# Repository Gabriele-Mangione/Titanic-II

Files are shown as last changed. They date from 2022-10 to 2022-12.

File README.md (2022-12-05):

# TITANIC II :ship:
TITANIC II is a project for an RC boat model with paired controller made by me! :grin:

## Working principle :gear:

Both electronics are powered using 14.4V Batteries, use Arduino Nano Every(s) as μController and communicate via LoRa using two RFM69HCW modules.
The Boat uses a 12V motor to swim and a servo-motor to steer, while the transmitter sends information gathered by a joystick module. 

## Features :bulb:
The boat is equipped with:
* A water gun controlled by a servomotor when clicking on the joystick
* Adjustable PWM motor speed
* Three HC-SR04 ultrasonic sensors that prevent hard collisions through adjusting of the motor speed
* External power supply pins for implementation of further modules (i.e. solar panels)

The transmitter is equipped with:
* Joystick module for a good user interface
* A tft 128x64 monochrome display to show inputs sent to the boat and boat connection
* Comfortable 3d-printed case

## Dependencies :scroll:
The codes need the following libraries in order to work.

Boat.ino:
* RFM69 lib (Lowpowerlab)
* SPI lib (Arduino)
* Servo lib (Arduino)
* [Ultrasonicsensor lib (made by me)](https://github.com/Gabriele-Mangione/UltrasonicSensor_lib)
  * you can find this in [my GitHub Repositories](https://github.com/Gabriele-Mangione?tab=repositories)

Transmitter.ino:
* GFX lib (Adafruit)
* SSD1306 lib (Adafruit)
* RFM69 lib (Lowpowerlab)
* SPI lib (Arduino)

## Contributing :pencil2:

You are welcome to make commits of suggestions for improvements.

## License :bookmark_tabs:

[MIT](https://choosealicense.com/licenses/mit/)

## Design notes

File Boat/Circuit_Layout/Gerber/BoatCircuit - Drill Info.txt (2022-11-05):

ULTIBOARD DRILL REPORT

Design: BoatCircuit

DRILL FILE SETTINGS
Excellon 2, Absolute, Metric, 3.4 

DEFINITION COPPER LAYERS
Copper Top
Copper Bottom

--------------------------------------------------------------------

DRILLFILE                                    LAMINATION
BoatCircuit - Copper Top-Copper Bottom.drl   Copper Top .. Copper Bottom

TOOL     SIZE   TYPE  COUNT
   1   3.2000   NPTH      4
   2   1.0000    PTH     72
   3   1.3208    PTH      3

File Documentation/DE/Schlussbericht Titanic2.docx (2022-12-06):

# TITANIC II

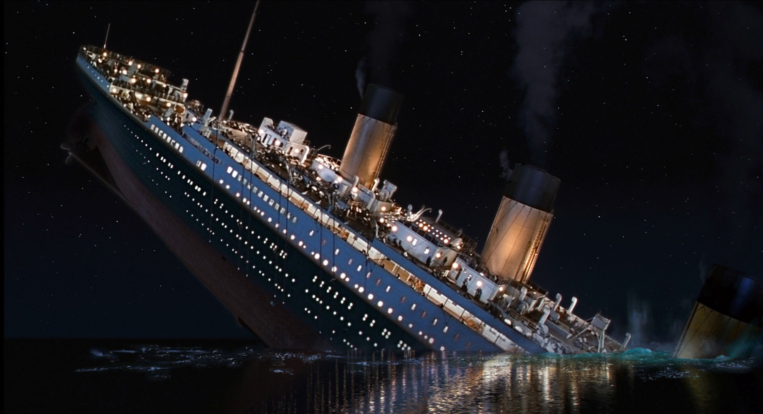
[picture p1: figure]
What's Jewish About … The Titanic? - Atlanta Jewish Times

Gabriele Mangione

ETRO 7A 2022
BüP Projekt

# Projektbeschreibung

Titanic 2 ist ein ferngesteuertes Modell-Boot. Der Rumpf besteht aus Holz und ist mit Holzlack gefertigt. Das Boot hat einen hohlen Raum, wo die ganze Elektronik installiert ist. Ein 12V Motor ist hier mit einem 3D-gedruckten Teil befestigt. Unterm Dach sind eine mechanische Pumpe und ein Servomotor befestigt, sodass die Umdrehung vom Servomotor, Wasser aus der Pumpe schiessen lässt. Ein zweiter Servomotor ist beim Heck des Bootes befestigt und steuert die Ruder. Beim Bug sind drei Ultraschallsensoren montiert, die die Distanz in drei verschiedene Richtungen messen. Ist die gemessene Distanz kleiner als 50 cm, wird die Geschwindigkeit vom Boot auf 20% der Eingabe beschränkt.

Der Transmitter vom Boot wurde 3D-Gedruckt und hat einen Joystick und ein Display als UI. Durch die Bewegung vom Joystick wird auf der Y-Achse die PWM vom Motor gesteuert und Auf der X-Achse die Steuerrichtung durch das Ruder eingestellt. Beim Klicken vom Joystick wird ein Wasserstrahl vom Boot-Dach geworfen. Aufs Display werden die Steuereingänge vom Joystick angezeigt, sowie die drei gemessenen Distanzen der Ultraschallsensoren.

## Merkmale

- Motor mit PWM
- Ruder durch Servomotor steuern
- Wasserpistole
- Controller mit Joystick und Display
- Fernsteuerung durch Radiofrequenz (915MHz)

## Realisierungskonzept

### Idee

Im Fach Werken, hatte ich vor einige Jahre in der Sekundastufe ein Modellboot gebaut. Das Boot war nur mit einem Motor, ein Schalter und zwei befestigte Ruder vorgelegt. Die Idee ist es, das Boot fernsteuerbar zu machen.

### Boot Material

Das Boot hat einen Holz-Rumpf und ist mit Holzlack gefertigt. Es hat einen hohlen Raum, wo die ganze Elektronik installiert wird. Ein 12V Motor ist hier mit einem 3D-gedruckten Teil befestigt. Zwei Metall-Ruder sind beim hinteren Teil vom Boot platziert. Die Schaltung wird durch eine 14.4V Batterie mit Spannung versorgt.

### Motor mit PWM

Motor durch PWM-Ausgang vom Arduino und N-MOS steuern. Durch die PWM-Einstellung kann man die Geschwindigkeit des Motors bzw. Boot einstellen.

### Ruder durch Servomotor steuern

Die Ruder des Bootes werden durch einen Servomotor gesteuert. Sie sind mit einem Stab zusammen angeschlossen, sodass beide Rudern durch einen Servomotor gesteuert werden können.

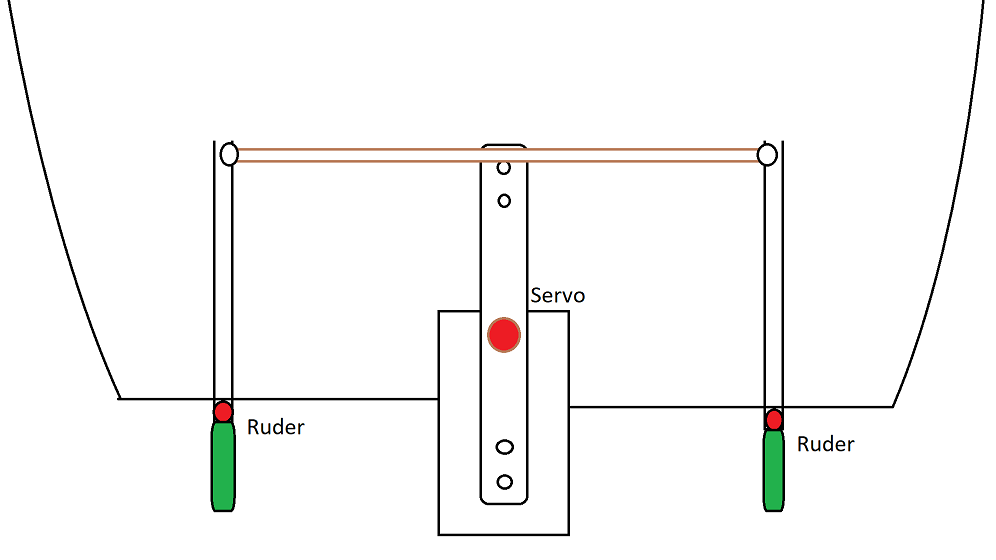
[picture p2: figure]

Abbildung 1: Ruder Mechanismus

### Wasserpistole

Für die Wasserpistole wird eine solche Pumpe verwendet:

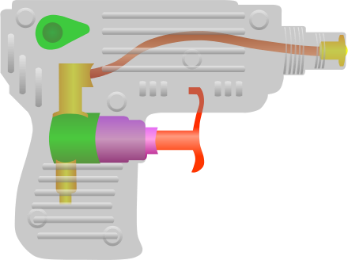
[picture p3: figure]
Water gun - Wikiwand

Abbildung 2: Pumpe Wasserpistole

An der Wassereingangsseite der Pumpe ist ein Schlauch, der ins Wasser über Bord liegt. So bekommt die Wasserpistole Flüssigkeit aus dem Wasserspiegel.

### Kommunikation

Die Kommunikation zwischen Boot und Transmitter passiert durch 915MHz Radio Module.

### Distanzsensoren

Um ungewollten Umfällen zu vermeiden, werden drei Distanzsensoren aufs Boot platziert. Falls die gemessene Distanz weniger als 50cm beträgt, wird das PWM vom Boot auf ein Fünftel vom Eingabewert beschränkt.

### Transmitter

Beim Transmitter werden ein Display und ein Joystick stehen, um das Boot zu steuern und die verschiedenen Parameter, wie PWM und Lenkwinkel angezeigt.

# Skizze zum Projekt

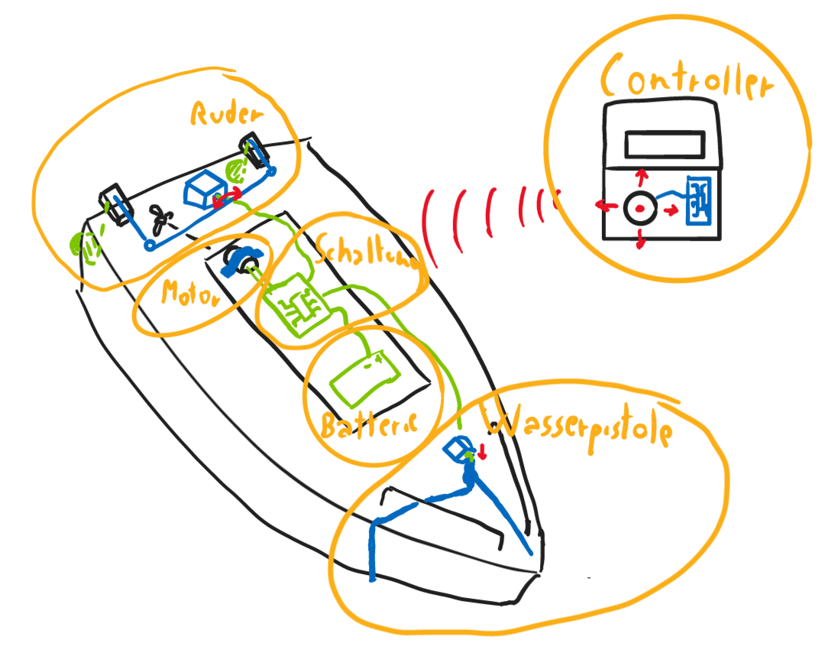
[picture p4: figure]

Abbildung 3: Projektskizze

# Blockschaltbild

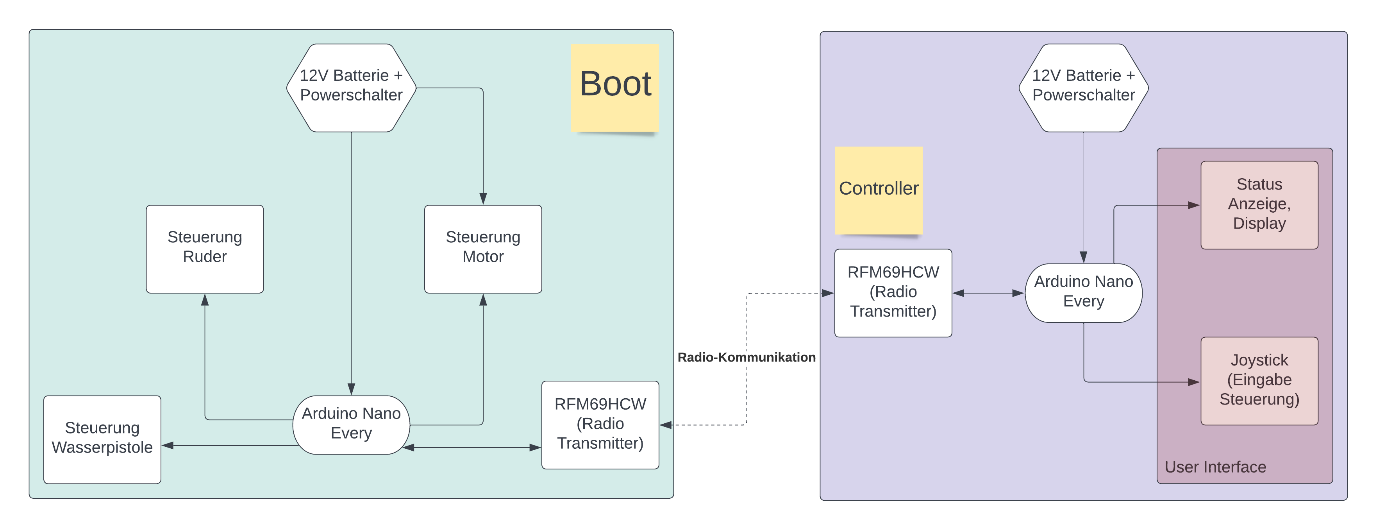
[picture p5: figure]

Abbildung 4: Blockschaltbild Architektur

# Schaltungen

## Bootschaltung

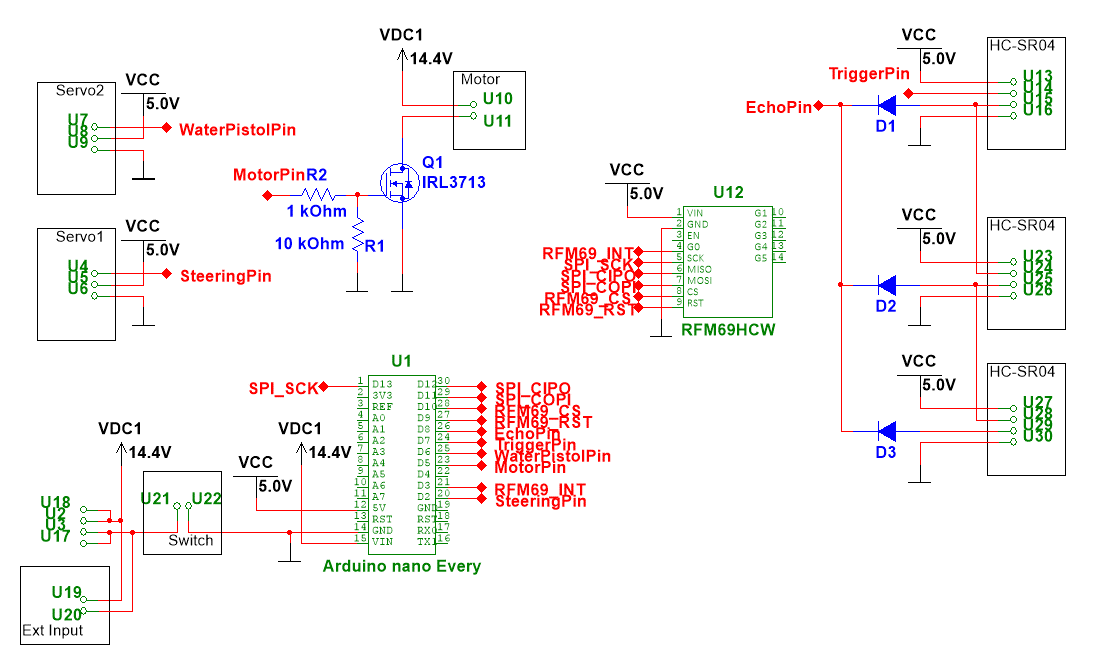
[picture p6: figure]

Abbildung 5: Bootschaltung

## Transmitterschaltung

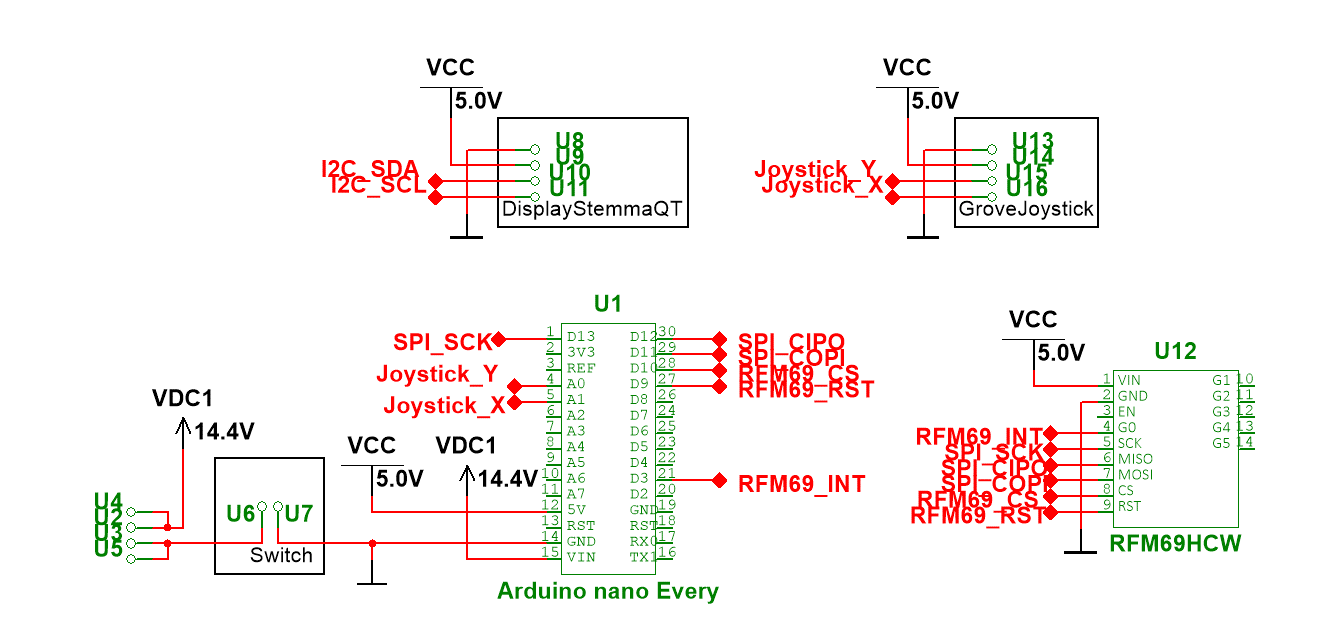
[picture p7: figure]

Abbildung 6: Transmitterschaltung

## Schaltungsbeschreibung

### Spannungsversorgung

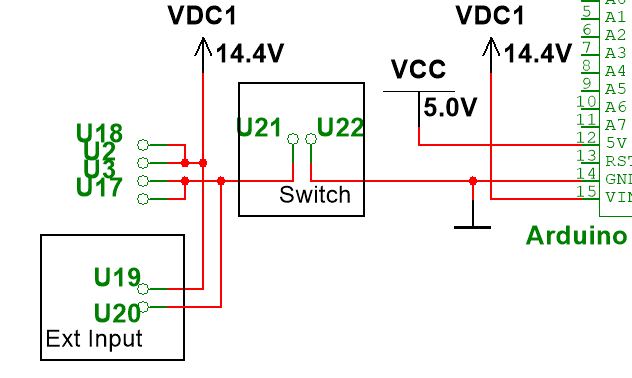
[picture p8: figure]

Abbildung 7: Spannungsversorgung Boot

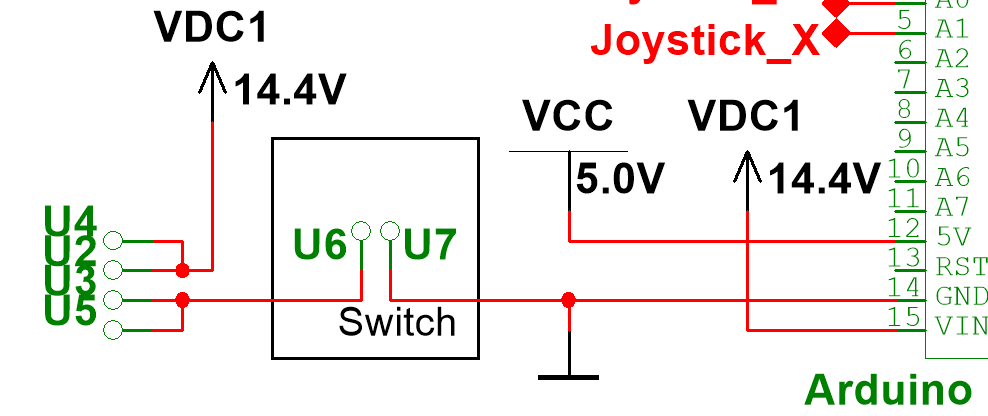
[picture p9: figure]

Abbildung 8: Spannungsversorgung Transmitter

Eine 14.4V 3200 mAh Li-Ion Batterie wird als Spannungsversorgung für die Schaltung gebraucht. Parallel zur Batterie hat es bei der Bootschaltung ein EXT Input, für eine eventuelle Power-Erweiterung, wie Solar Panels. Die Ground-Leitung wird durch einen Powerschalter getrennt, um die Schaltung manuell abschalten zu können. Die 14.4V Versorgungsspannung wird durch den im Arduino integrierten Spannungsregler auf 5.0V geregelt und beim Entsprechenden Pin vom uC ausgegeben.

### Mikrocontroller

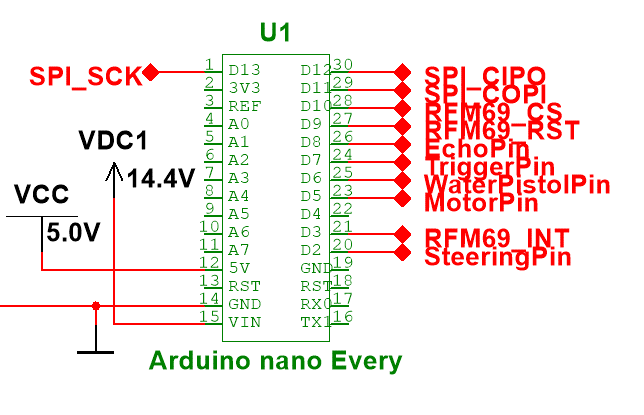
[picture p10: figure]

Abbildung 9: Schaltung Arduino Nano Every

Als Mikrocontrollereinheit werden bei den Schaltungen zwei Arduino Nano Every eingesetzt. Diese steuern die ganze Logik der Schaltungen. Siehe Code für genauere Beschreibung

### Radiomodul

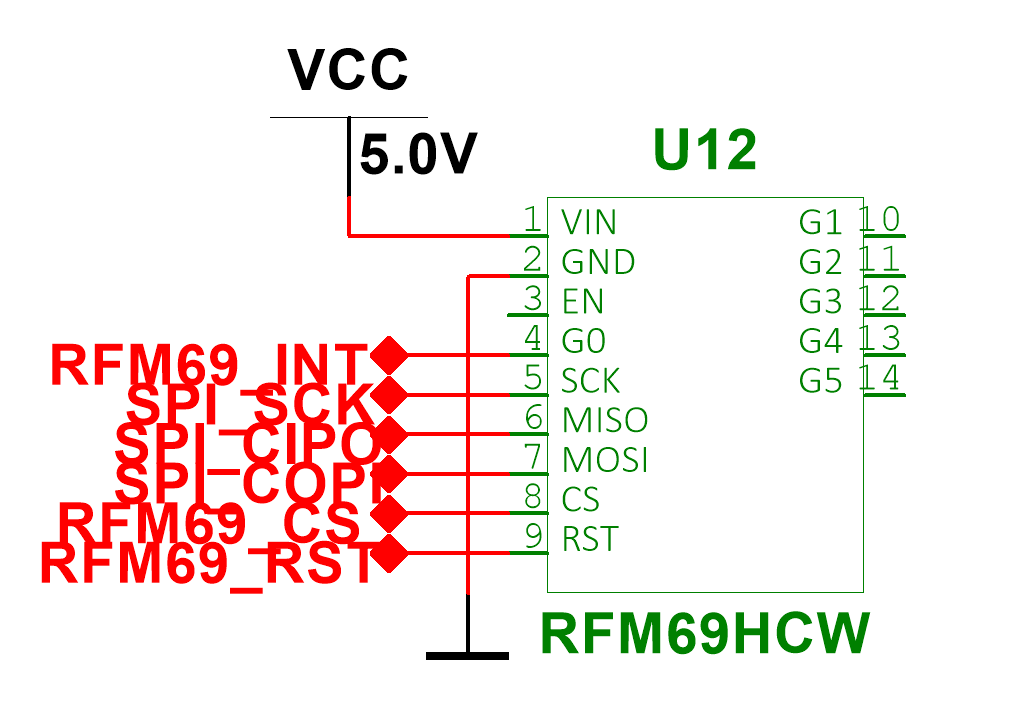
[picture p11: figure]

Abbildung 10: Radiomodul

Als Radiokommunikationsmodul wird ein RFM69HCW LoRa Radio Modul von Adafruit verwendet. Dieses Modul kommuniziert im Frequenzbereich von zwischen 868MHz und 915MHz mit bis zu 100mW Power-Output. Die Kommunikation zwischen Arduino und Radiomodul passiert durch SPI-Protokoll. Durch die RFM69_RST Leitung kann man das Modul durch einfaches Hoch- und Tiefsetzen der Spannung resetten und die RFM69_INT Leitung dient zur Synchronisierung der Operationen des Radiomodules durch Hardwareinterrupts.

Die Inputs vom Transmitter werden durch dieses Bauteil zum Boot kommuniziert und danach verarbeitet.

### Ausgangstufe Motor (Bootschaltung)

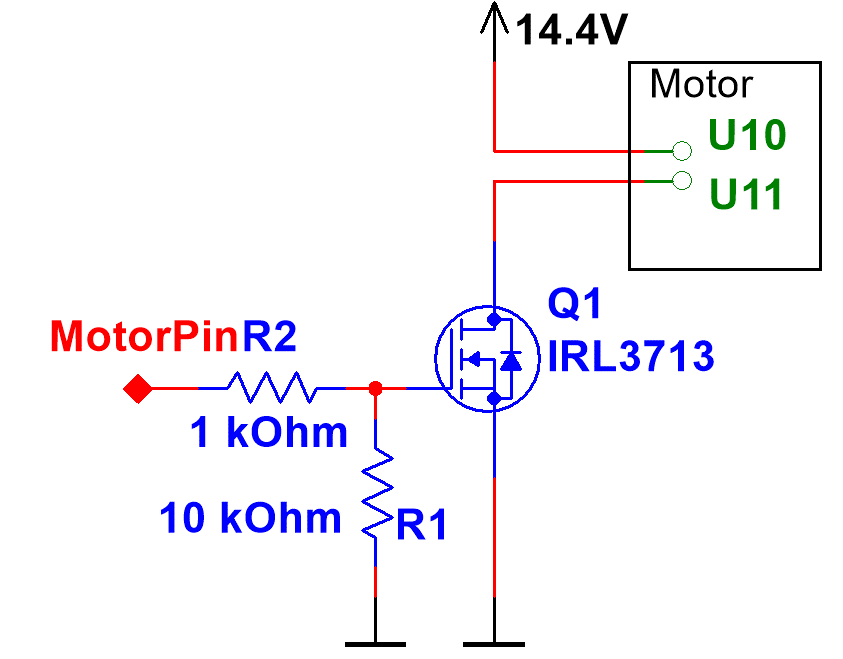
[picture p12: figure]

Abbildung 11: Ausgangstufe Motor

Die Ausgangstufe wird durch einen 2N7000 N-Mos Transistor gesteuert, der einen Pol vom Motor auf Ground zieht. Das Gate vom Transistor wird durch einen 1kOhm Schutzwiderstand vom Arduino mit einem PWM-Signal gesteuert. Ein 10kOhm Pull-Down Widerstand wird auch eigesetzt, um das Gate-Signal nicht auf Floating zu lassen. Der Duty-Cycle vom PWM-Signal wird vom Joystick der Transmitterschaltung bestimmt.

### Servomotoren (Bootschaltung)

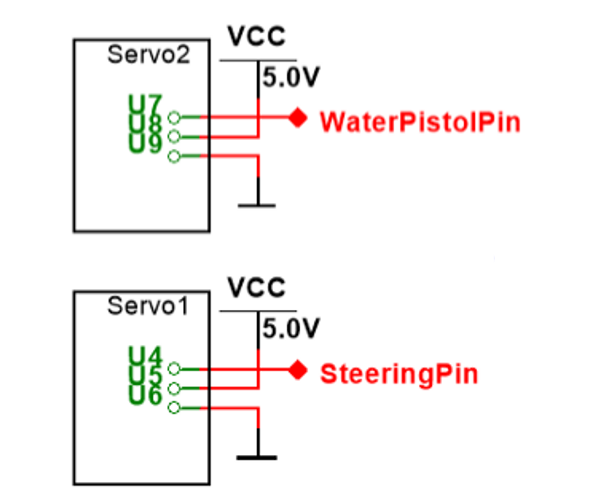
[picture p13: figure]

Abbildung 12: Servoschaltung

Zwei Servomotoren haben beim Boot die Aufgaben, die Ruder und die Wasserpistole zu steuern. Beide werden durch zwei PWM-fähige Arduino digital Pins gesteuert. Der Servo1 (Rudersteuerung) dreht sich von 45° auf 135° je nach Input vom Joystick und der Servo2 (Wasserpistolensteuerung) wechselt zwischen 0° und 45° mit dem Klicken vom Joystick.

### Ultraschalldistanzsensoren (Bootschaltung)

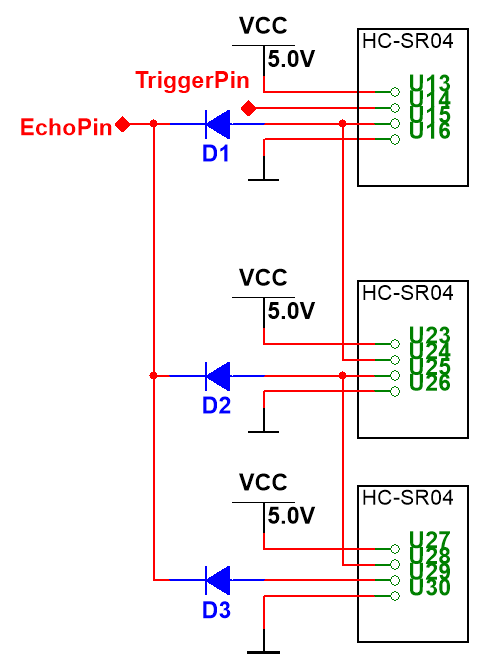
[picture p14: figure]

Abbildung 13: Ultraschallsensorschaltung

Hier werden drei HC-SR04 Ultraschallsensoren gesteuert.

Die einzelne Sensoren funktionieren folgendermassen:

Als erstes wird beim Trigger-Pin des Modules ein HIGH-Signal von mindestens 10 µs eingegeben. Das HC-SR04 wird dann automatisch eine 40kHz Schallwelle durch den Lautsprecher senden und danach das Echo-Pin auf HIGH setzen. Sobald das Mikrofon vom Modul das Ausgegebene 40kHz Signal einliest, wird die Spannung auf das Echo-Pin wieder auf LOW gesetzt. Mit der Zeit vom HIGH-Impuls beim Echo-Pin kann man die Zeit ausrechnen, die das Signal gebraucht hat, um zurückzukommen.

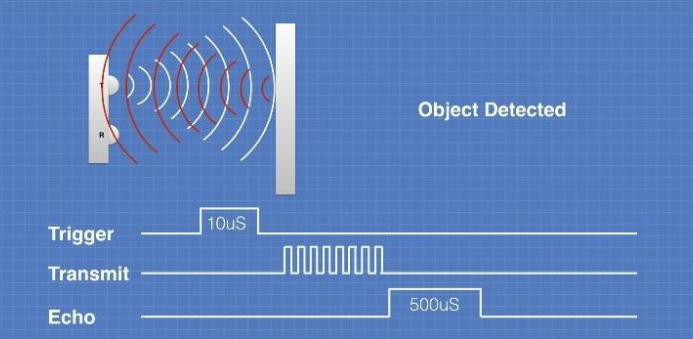
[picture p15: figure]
HC-SR04 Ultrasonic Distance Sensor with Arduino | DroneBot Workshop

Abbildung 14: HC-SR04 Signale

Um mehrere HC-SR04 Module auf einem Mal zu brauchen und somit weniger Arduino-Pins und Code-Zeilen zu verschwenden wurden die Ultraschallsensor-Module bei der Bootschaltung so zusammen angeschlossen:

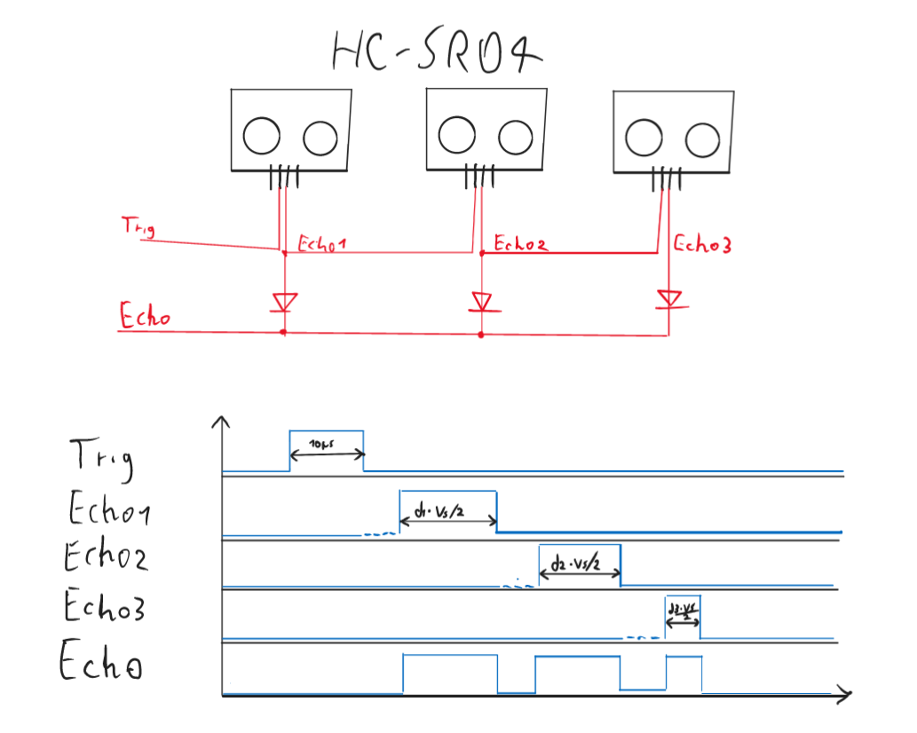
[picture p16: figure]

Abbildung 15: Spannung-Zeit-Diagramm Schaltung HC-SR04 Signale

Hier wird nur der Trigger-Pin vom ersten Modul gesteuert. Das Echo-Signal vom ersten ist mit dem Trigger-Pin vom zweiten Modul angeschlossen und steuert somit automatisch das zweite Modul. Das dritte Modul wird wie das zweite angesteuert. Alle Echo-Pins werden durch Dioden zusammengeschlossen und danach vom Arduino gemessen. Durch diese Verbindungen triggert das erste Modul automatisch das zweite und das zweite automatisch das dritte.

Diese Schaltung ist modular und macht es möglich, sehr einfach neue Module einzufügen.

### Joystick (Transmitterschaltung)

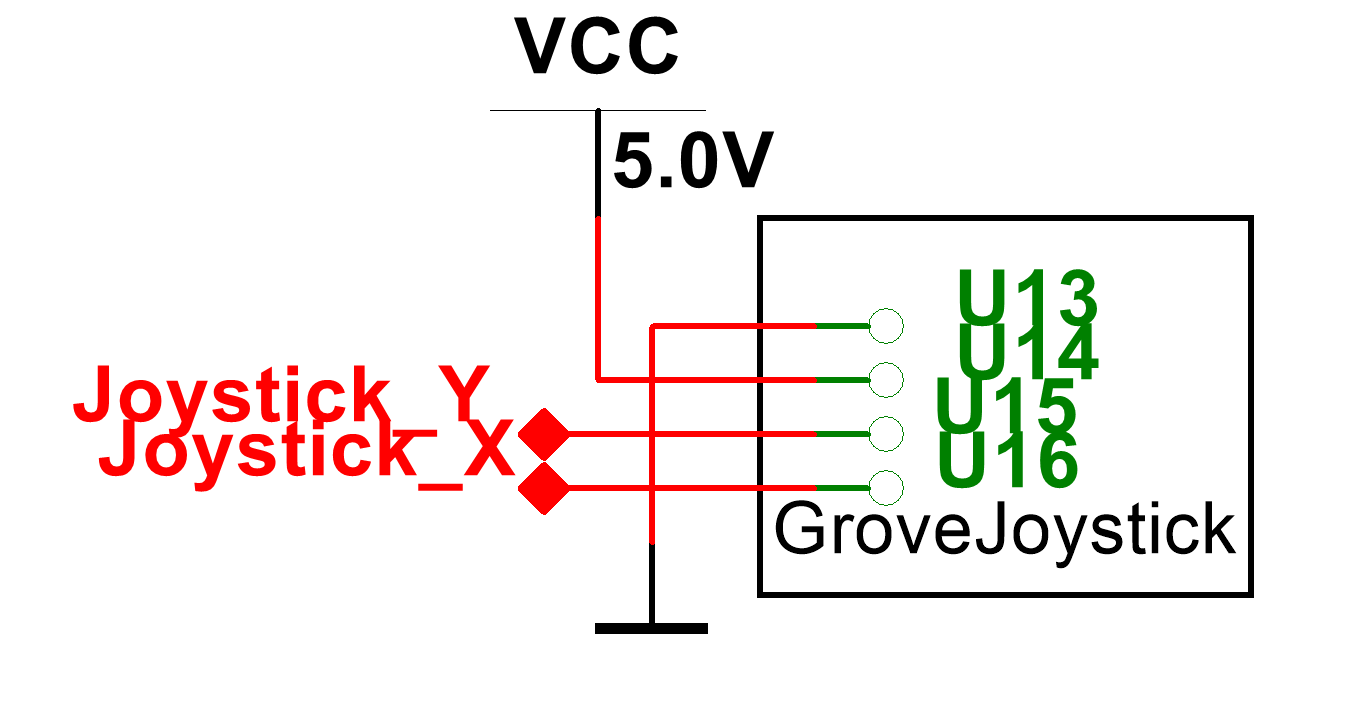
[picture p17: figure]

Abbildung 16: Joystick Schaltung

Für die Eingabe bei der UI vom Transmitter wird ein Joystick eingesetzt. Dieser besteht aus zwei Potenziometer und einen Taster. Die Zwei Output Pins werden analog vom Arduino gelesen. Die vom Arduino gelesene analoge Werte gehen von 200 bis zu 800 bei Bewegungen in den zwei Achsen. Sobald auf dem Joystick gedrückt wird, geht der analoge Wert der X-Achse auf 1023, da der Pin einfach auf VCC geschalten wird.

### Display (Transmitterschaltung)

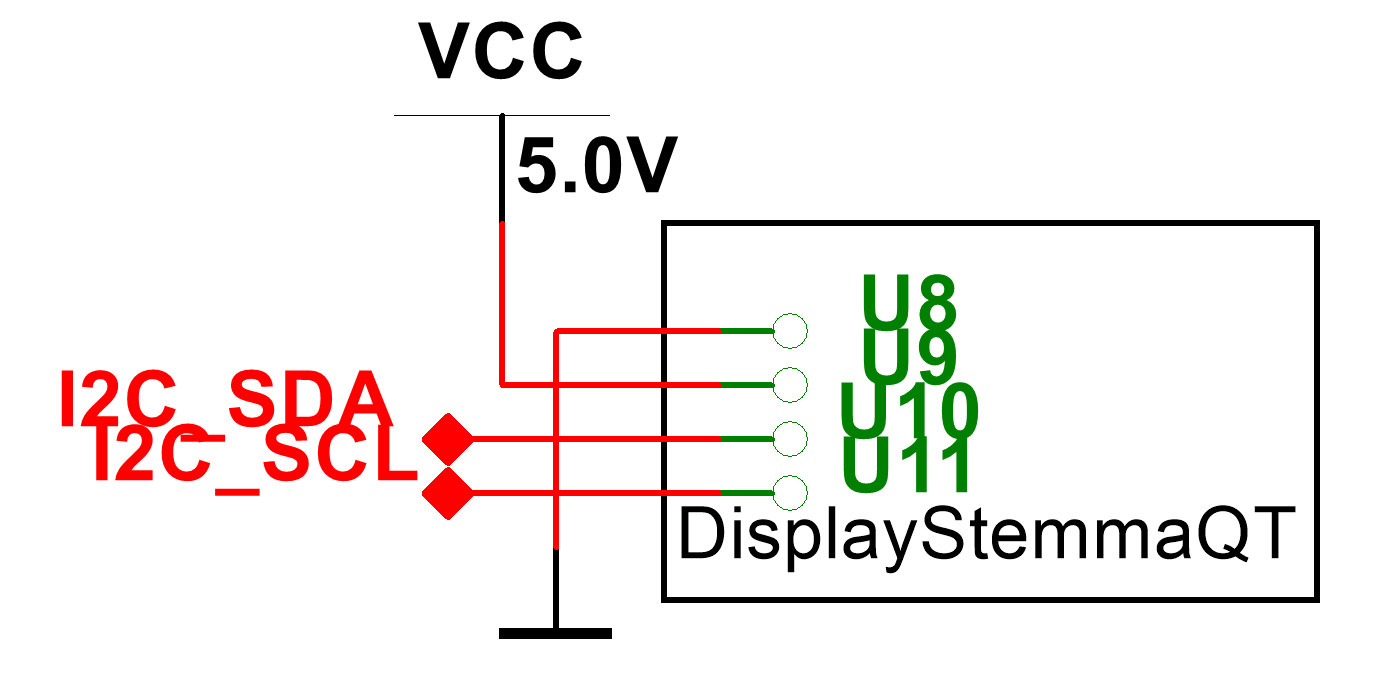
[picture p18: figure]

Abbildung 17: Display Stemma Schaltung

Bei der UI werden die Eingänge zusammen mit den Distanzen der Ultraschallsensoren auf einem Display angezeigt. Für diesen Zweck wird ein SSD1306 OLED Monochrom Adafruit Display angewendet. Dieses Modul hat eine I2C Schnittstelle und wird entsprechend vom Arduino gesteuert.

# Layout

## Boot

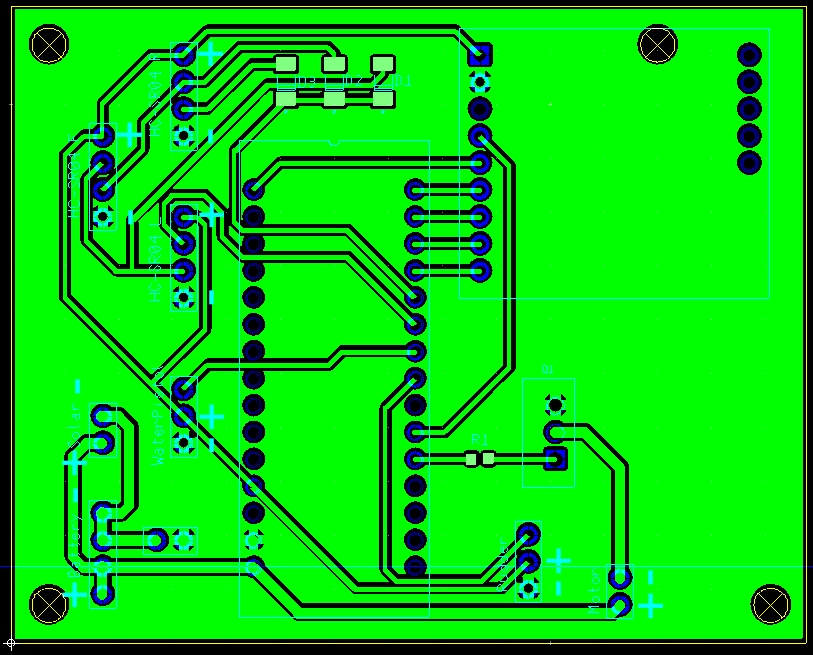
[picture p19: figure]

Abbildung 18: Boot Layout

## Transmitter

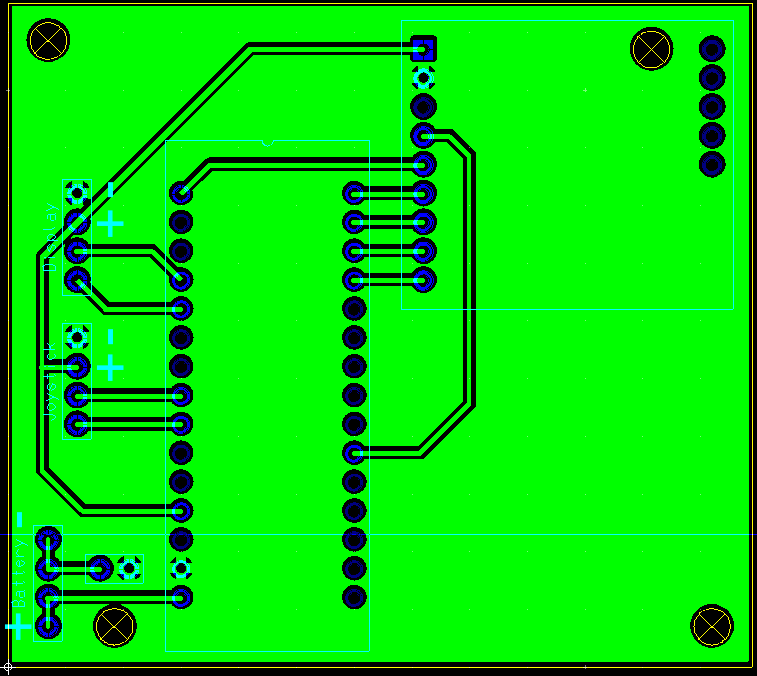
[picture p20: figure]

Abbildung 19: Transmitter Layout

# Code

Für das Projekt habe Ich eine GitHub Repo hergestellt. Hier findet man die Unterlagen des Projekts inkl. Code:

Gabriele-Mangione/Titanic-II (https://github.com/Gabriele-Mangione/Titanic-II)

# Materialliste

Anzahl | Bezeichnung | Typ | Schaltung | Link
2 | Arduino Nano Every | Arduino Nano Every | Boot & Transmitter | Arduino Nano Every (https://www.reichelt.com/ch/de/arduino-nano-every-atmega4809-ohne-header-ard-nano-eve-p261300.html?PROVID=2808)
2 | Radio Transceiver | Adafruit RFM69HCW | Boot & Transmitter | RFM69HCW (https://www.distrelec.ch/en/rfm69hcw-radio-transceiver-breakout-868mhz-915mhz-adafruit-3070/p/30139115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)
2 | 12V Akku | 12V 3200mAh | Boot & Transmitter | Marshall Stockwell 12V Akku (https://www.reichelt.com/ch/de/ersatzakku-marshall-stockwell-li-ion-3200-mah-akku-31260-p313225.html?r=1)
3 | Ultraschallsensor | HC-SR04 | Boot | HC-SR04 (https://www.distrelec.ch/de/ultraschall-abstandssensor-hc-sr04-sparkfun-electronics-sen-15569/p/30160395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)
2 | Servomotor | Q4 | Boot | Servo Q4 (https://www.reichelt.com/ch/de/servo-q4-standard-jamara-033217-p270932.html?&nbc=1)
1 | 12V Motor | 12V Motor | Boot | PEL00882 12V Motor (https://ch.farnell.com/pro-elec/pel00882/dc-motor-high-power-12v/dp/3383476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)
1 | N-MOS Transistor | 2N7000 | Boot
1 | 10k Widerstand | 0603 10k | Boot
1 | 1k Widerstand | 0603 1k | Boot
3 | Diode | 1N4000 | Boot
1 | Switch | ON-OFF | Boot
1 | LCD | Adafruit Monochrome 0.96" 128x64 OLED Graphic Display | Transmitter | Adafruit TFT-LCD-Display (https://www.adafruit.com/product/326)
1 | Joystick | Seeed Studio Grove | Transmitter | Seeed Studio Grove Joystick (https://www.distrelec.ch/de/grove-daumen-joystick-seeed-studio-101020028/p/30069811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)

# Zeitplanung & Stand der Arbeiten

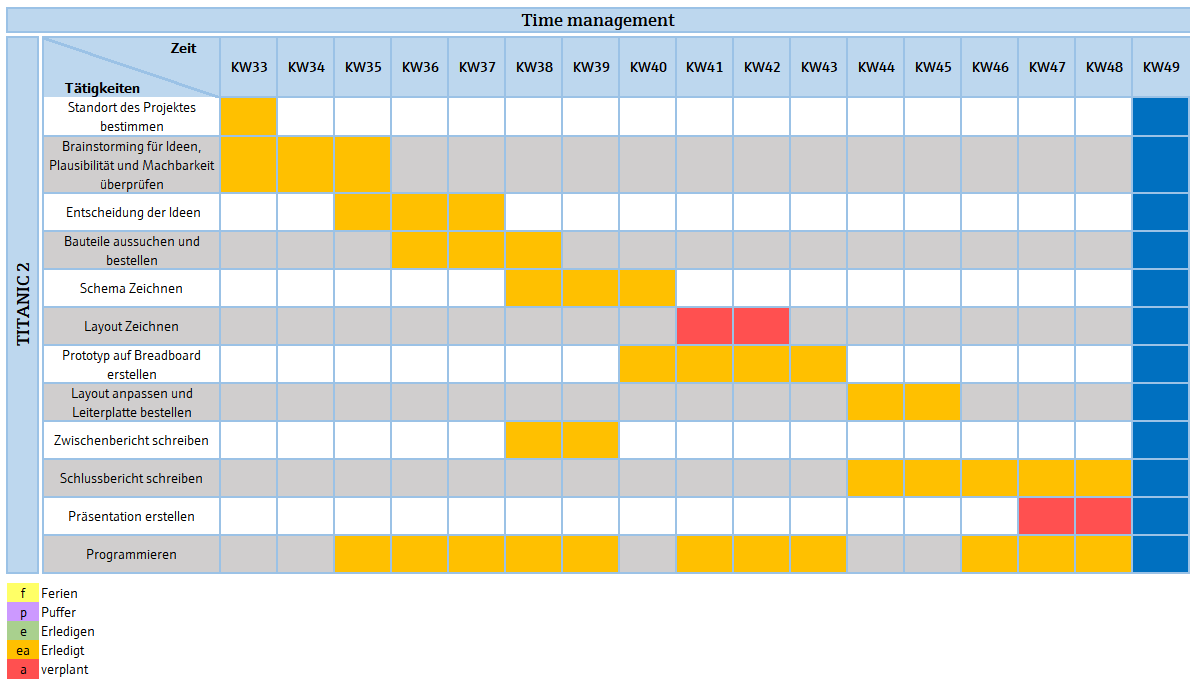
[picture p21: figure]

Abbildung 20: Zeitplan

# Fazit

TITANIC 2 war eine gute Projektidee, die meinem Wissenstand erweitert hat. Es ist aber auch ein cooles und lustiges Projekt für meine Freizeit gewesen.

Das Projekt ist erfolgreich abgeschlossen, hat aber auch Verbesserungspotenzial. Aus diesem Grund habe ich es so einfach erweiterbar wie möglich gemacht. Ein weiteres Vorgehen wäre z.B. ein Solarmodul beim Boot zu implementieren. Ausserdem sind Software-Updates immer möglich.

BüP Projekt ETRO 7A 2022 Gabriele Mangione

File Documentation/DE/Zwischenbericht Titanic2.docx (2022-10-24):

# TITANIC II

# Projektbeschreibung

Titanic 2 ist ein ferngesteuertes Modell-Boot. Der Rumpf besteht aus Holz und ist mit Holzlack gefertigt.

## Merkmale

- Motor mit PWM
- Ruder durch Servomotor steuern
- Falls möglich Wasserpistole
- Controller mit Joystick
- Fernsteuerung durch Radiofrequenz (400MHz - 900MHz)

## Realisierungskonzept

### Boot Material

Das Boot hat einen Holz-Rumpf und ist mit Holzlack gefertigt. Es hat einen hohlen Raum, wo die ganze Elektronik installiert wird. Ein 12V Motor ist hier mit einem 3D-gedruckten Teil befestigt. Zwei Metall-Ruder sind beim hinteren Teil vom Boot platziert.

### Motor mit PWM

Motor durch PWM-Ausgang vom Arduino und N-MOS steuern. Durch PWM-Einstellung kann man die Schnelligkeit des Motors bzw. Boot einstellen.

### Ruder durch Servomotor steuern

Die Ruder des Bootes werden durch einen Servomotor gesteuert. Sie sind mit einem Stab zusammen angeschlossen, sodass beide Rudern durch einen Servomotor gesteuert werden können.

### Wasserpistole

Die Idee ist, eine Pumpe aus einer Wasserpistole auf das Boot zu montieren und mit einem Servomotor zu steuern. Ein Schlauch kann dann aus der Pumpe bis zum Boden des Bootes gezogen werden, um dieselbe Flüssigkeitsreserve wie Schwimmoberfläche zu brauchen. Diese Idee ist zusätzlich und wird nur umgesetzt, falls es dafür Zeit hat.

### Controller mit Joystick

Die Steuerung vom Boot passiert durch einen Controller mit Joystick. Mit dem Joystick kann man den Rudern und den Motor steuern und durch das Klicken wird Wasser aus der Wasserpistole geschossen. Ausserdem ist auf dem Controller noch ein Power-Schalter.

# Skizze zum Projekt


# Blockschaltbild

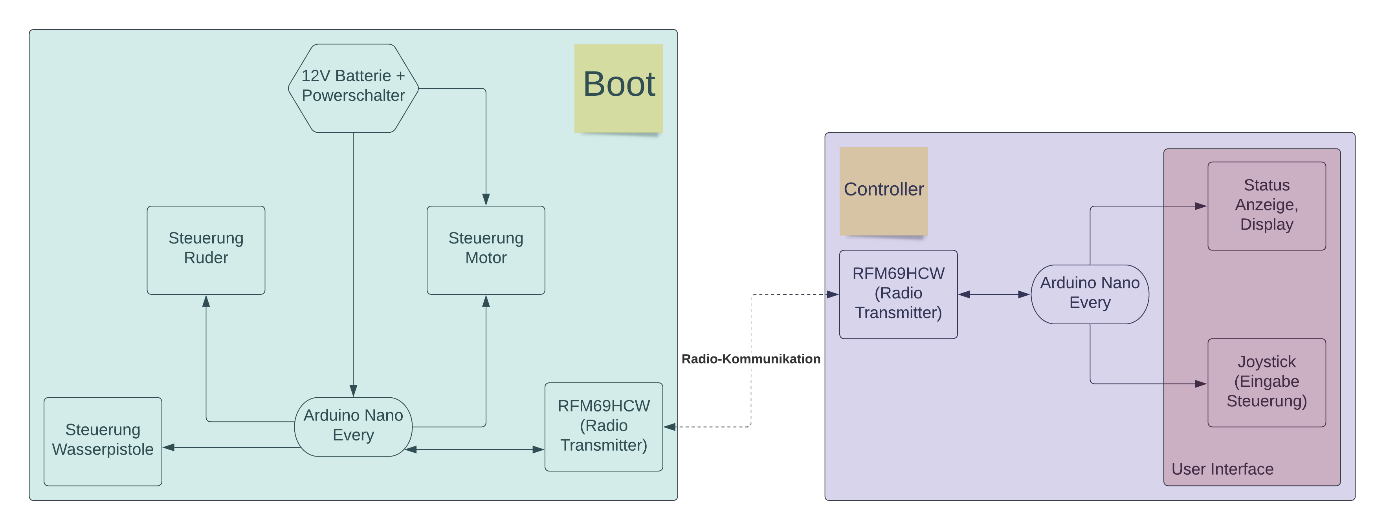
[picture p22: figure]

# Zeitplanung

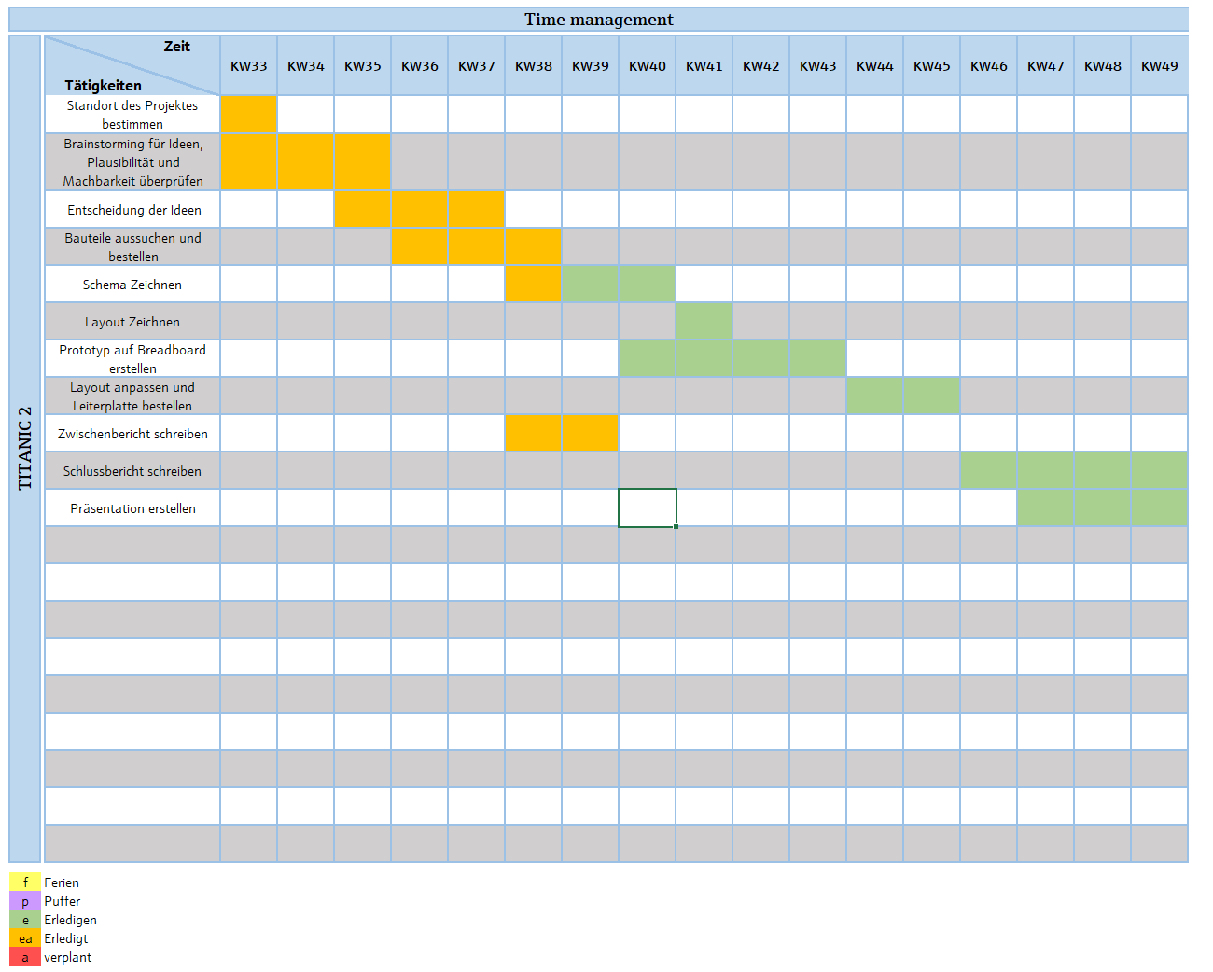
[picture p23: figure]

BüP Projekt ETRO 7A 2022 Gabriele Mangione

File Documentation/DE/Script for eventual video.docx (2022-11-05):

Hi, welcome to *channel name*

In this video, I will showcase one of my latest projects.

It is a radio-commanded wooden boat with coupled controller. I called it “Titanic II”.

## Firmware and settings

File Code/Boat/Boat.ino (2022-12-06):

#include <RFM69.h>
#include <SPI.h>
#include <Servo.h>
#include <Ultrasonicsensor.h>


#define SERVOPIN 2
#define WATERPISTOLPIN 6
#define MOTORPIN 5

//Radio module pins
#define RFM69_RST 9
#define RFM69_CS 10
#define RFM69_INT 3

//Radio IDs
#define NETWORKID 0  // Must be the same for all nodes
#define MYNODEID 3   // My node ID

//Ultrasound sensor pins
#define TRIGGERPIN 7
#define ECHOPIN 8

#define MAX_DISTANCE 500


// prototypes
void steer(uint8_t deg);
void motorPWM(int8_t dutyCycle);
bool timeoutReceiver(unsigned long stoptime);

Servo SteeringServo;
Servo WaterPistol;

RFM69 Radio(RFM69_CS, RFM69_INT);

UltrasonicSensorArray DistanceSensors(TRIGGERPIN, ECHOPIN, 3);

void setup() {
  //for testing
  //Serial.begin(9600);

  //set pin modes
  pinMode(MOTORPIN, OUTPUT);
  pinMode(TRIGGERPIN, OUTPUT);
  pinMode(ECHOPIN, INPUT);
  pinMode(RFM69_RST, OUTPUT);

  digitalWrite(MOTORPIN, LOW);
  digitalWrite(RFM69_RST, LOW);

  //Assign servo pins to servo objects
  WaterPistol.attach(WATERPISTOLPIN);
  SteeringServo.attach(SERVOPIN);
  SteeringServo.write(90);

  //Radio init
  // manual Radio reset
  digitalWrite(RFM69_RST, HIGH);
  delay(10);
  digitalWrite(RFM69_RST, LOW);
  delay(10);

  while (!Radio.initialize(RF69_915MHZ, MYNODEID, NETWORKID)) {
    Serial.println("RFM69 Radio init failed");
  }
  Radio.setHighPower();
}

void loop() {
  //standard values, in case no inputs are received from radio
  uint8_t inputMotorSpeed = 100;
  uint8_t inputSteerAngle = 45;

  uint16_t distances[3];
  DistanceSensors.getSensorDistance(distances);

  //if an object within 500mm is detected
  if (distances[0] < MAX_DISTANCE || distances[1] < MAX_DISTANCE || distances[2] < MAX_DISTANCE) {
    inputMotorSpeed /= 5;
  }

  distances[0] /= 100;
  distances[1] /= 100;
  distances[2] /= 100;
  //if signal is received
  if (Radio.receiveDone()) {
    //send distances to transmitter
    Radio.sendWithRetry(4, distances, 3, 2, 20);
    //overwrite standard values with read values
    inputMotorSpeed = Radio.DATA[0];
    inputSteerAngle = Radio.DATA[1];
  }

  motorPWM(inputMotorSpeed);
  //if a click on the joystick is detected
  if (inputSteerAngle > 100) {
    WaterPistol.write(40); //spray watergun
  }
  else {
    steer(inputSteerAngle);
    WaterPistol.write(0); //reset watergun
  }
}

/**
 *  in Degrees°, 0 - 60
 *  steer from 60° to 120°
 */
/**
 * @brief steer in angle "deg"
 * 
 * @param deg degrees 0-90, where 45 is forward
*/
void steer(uint8_t deg) {
  if (deg > 90) {
    deg = 90;
  }
  SteeringServo.write(45 + deg);
}

/**
 * @brief set speed value for motor using PWM
 * 
 * @param dutyCycle 0-200, where 0 is full backwards power, 100 is no movement and 200 is full forwards power
 */
void motorPWM(int8_t dutyCycle) {
  if (dutyCycle > 200) {
    dutyCycle = 200;
  }
  if (dutyCycle < 100) {
    dutyCycle = 100;
  }
  dutyCycle = dutyCycle - 100;
  analogWrite(MOTORPIN, dutyCycle * 2.55);
}
/**
 * @brief check for a certain time if the Radio received a new message
 * 
 * @param stoptime time in ms of duration 
 * @return true when a message was received
 * @return false when stoptime has passed and no message was received
 *
bool timeoutReceiver(unsigned long stoptime) {
  unsigned long time = millis();
  while (millis() - time < stoptime) {
    if (Radio.receiveDone()) {
      return true;
    }
    // yield();
  }
  return false;
}
*/

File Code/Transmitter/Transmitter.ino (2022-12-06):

#include <Adafruit_GFX.h>
#include <Adafruit_SSD1306.h>
#include <RFM69.h>
#include <SPI.h>

//Display settings
#define SCREEN_WIDTH 128  // OLED display width, in pixels
#define SCREEN_HEIGHT 64  // OLED display height, in pixels
#define SCREEN_ADDRESS 0x3D
#define OLED_RESET -1

//Radio module pins
#define RFM69_RST 9
#define RFM69_CS 10
#define RFM69_INT 3

//Radio IDs
#define NETWORKID 0  // Must be the same for all nodes
#define MYNODEID 4   // My node ID

//prototypes
bool sendWithResponse(uint16_t toAddress, const void* buffer, uint8_t bufferSize, uint8_t retries, uint8_t retryWaitTime);

RFM69 radio(RFM69_CS, RFM69_INT);
Adafruit_SSD1306 display(SCREEN_WIDTH, SCREEN_HEIGHT, &Wire, OLED_RESET);

void setup() {
    //for testing
    //Serial.begin(9600);

    //set pin modes
    pinMode(RFM69_RST, OUTPUT);

    digitalWrite(RFM69_RST, LOW);

    //display init
    while (!display.begin(SSD1306_SWITCHCAPVCC, SCREEN_ADDRESS)) {
        Serial.println("SSD1306 allocation failed");
    }
    delay(1000);
    display.clearDisplay();
    display.setTextSize(1);
    display.setTextColor(1);

    // RFM69 Radio init
    // manual Radio reset
    digitalWrite(RFM69_RST, HIGH);
    delay(10);
    digitalWrite(RFM69_RST, LOW);
    delay(10);

    while (!radio.initialize(RF69_915MHZ, MYNODEID, NETWORKID)) {
        Serial.println("RFM69 radio init failed");
    }
    radio.setHighPower();
}

void loop() {
    //read joystick values
    uint8_t outputMotorSpeed = map(analogRead(A0), 249, 772, 0, 200); //y axis
    uint8_t outputSteerAngle = map(analogRead(A1), 248, 775, 0, 90); //x axis

    //create buffer to send values via radio
    uint8_t buf[2] = { outputMotorSpeed, outputSteerAngle };
    uint8_t sensorDistances[3] = { 0 };

    //send and retry until a response has come
    if (sendWithResponse(3, buf, 2, 10, 20)) {
        radio.sendACK();
        //save distance values
        sensorDistances[0] = radio.DATA[0];
        sensorDistances[1] = radio.DATA[1];
        sensorDistances[2] = radio.DATA[2];
    }

    //display values
    display.clearDisplay();
    display.setCursor(0, 5);
    display.print("Motor Speed:     ");
    display.print(outputMotorSpeed - 100);
    display.setCursor(120, 5);
    display.println("%");
    display.print("Steering Angle:  ");
    display.print(outputSteerAngle + 45);
    display.setCursor(120, 11);
    display.println("o");
    display.setCursor(0, 32);
    display.print("Distance 0:  ");
    display.println(sensorDistances[0]);
    display.print("Distance 1:  ");
    display.println(sensorDistances[1]);
    display.print("Distance 2:  ");
    display.println(sensorDistances[2]);

    display.display();
}

/**
 * @brief send data and retry until getting a response back, in this case containing the sensor distances
 * 
 * @param toAddress adress of receiver radio
 * @param buffer data array to send
 * @param bufferSize size of data array
 * @param retries  how many times to retry sending
 * @param retryWaitTime how much time between retries in ms
 * @return true if a response has successfully been received
 * @return false when time is up and yet no responce has come
 */
bool sendWithResponse(uint16_t toAddress, const void* buffer, uint8_t bufferSize, uint8_t retries, uint8_t retryWaitTime) {
    uint32_t sentTime;
    for (uint8_t i = 0; i <= retries; i++) {
        radio.send(toAddress, buffer, bufferSize, true);
        sentTime = millis();
        while (millis() - sentTime < retryWaitTime) {
            if (radio.receiveDone()) return true;
        }
    }
    return false;
}

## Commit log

2022-10-25 boat update
    changed boat uC to Arduino nano every,
    Servo Timer2 library back to standard Servo library.
2022-10-27 added documentation
    [Time management.xlsx]
2022-10-31 Updated Documentation
    [Time management.xlsx]
2022-10-31 Circuit update
2022-11-01 Circuit updated
2022-11-03 Finished layout
    [BoatCircuit - Copper Top-Copper Bottom.drl, TransmitterCircuit - Copper Top-Copper Bottom.drl, TransmitterCircuit - Lötstoppmaske oben.gbr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]
2022-11-09 last version of circuit
    [BoatCircuit - Board Outline.gbr, BoatCircuit - Bohrungssymbole-Copper Top-Copper Bottom.gbr, BoatCircuit - Copper Bottom.gbr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]
2022-11-09 fix for motor pwm
    [Boat.ino]
2022-11-29 analog write bug fix
    [Boat.ino]
2022-11-29 added Pulldown Resistor to Motor Control
2022-12-05 rearranged structure
    [Time management.xlsx]
2022-12-06 Added Documentation DE
    [Time management.xlsx]
